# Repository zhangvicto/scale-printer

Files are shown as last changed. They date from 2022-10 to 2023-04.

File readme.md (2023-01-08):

# Particle Swarm Optimization of 3D Printing Parameters on Open-Source Commercial 3D Printer

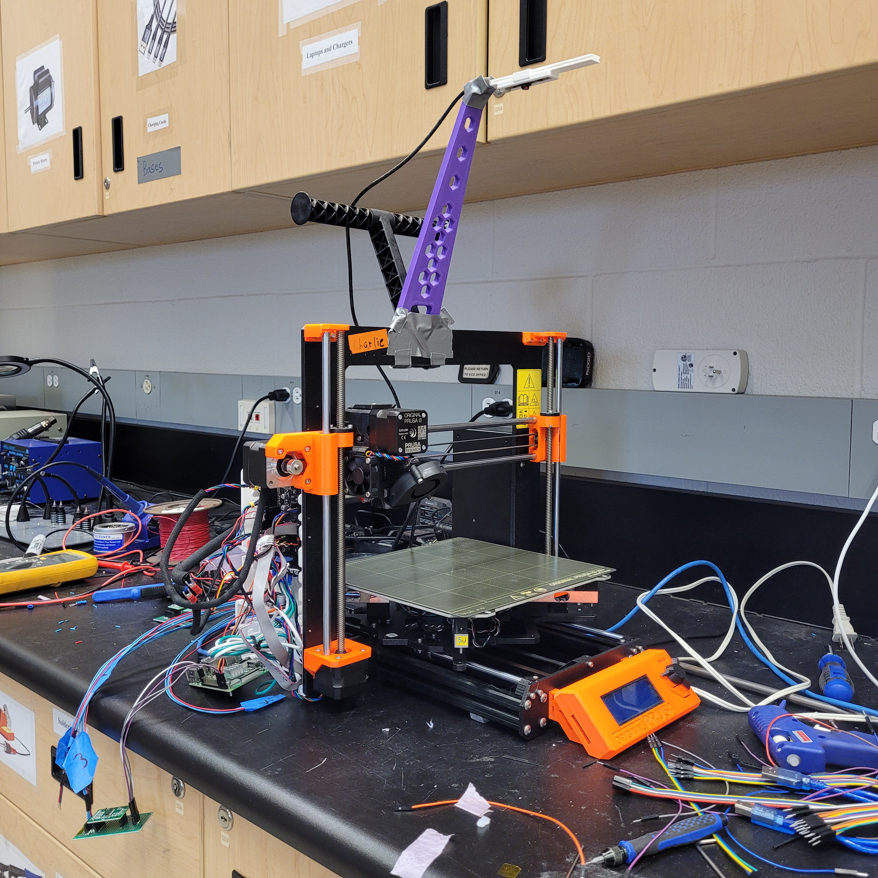
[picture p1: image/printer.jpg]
printer


# Current Progress
- [x] Mechanical Design
- [x] Test Load Cells
- [x] Test Camera
- [ ] Test Dimensional Measurement {80%}
- [ ] PSO Implementation {90%}
- [ ] Documentation {50%}

## Additional Features 
- [ ] Web Server {5%}
- [ ] Refinement {5%}

# Hardware
## Mechanical Design
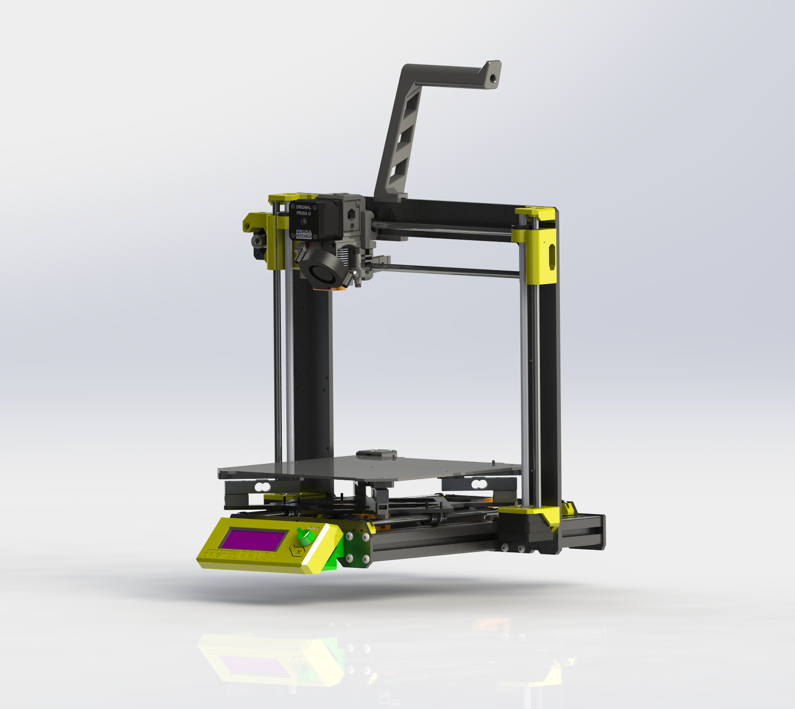
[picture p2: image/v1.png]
v1

The mechanical is designed around the Prusa MK3s, as it is a versatile printer that can be easily modified. Load cells and a camera were mounted on the printer using 3D printed parts. 

Load Cell Configuration: 
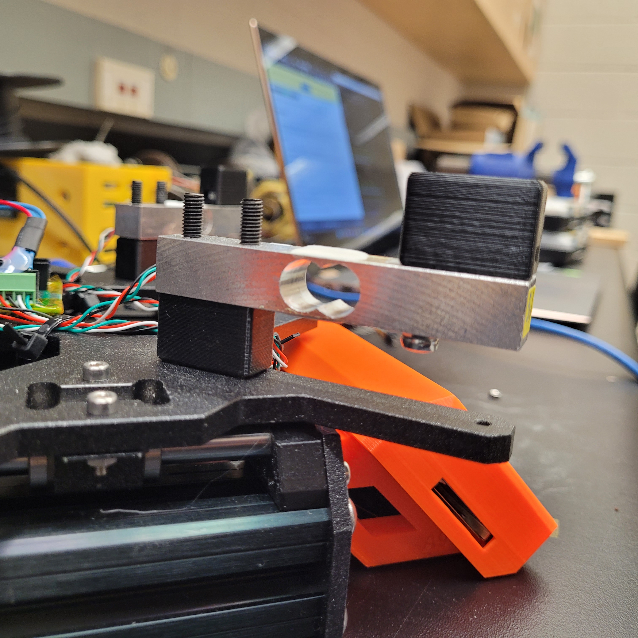
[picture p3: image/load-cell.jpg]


## Bill of Materials
Found in repo. 
Total cost excluding printer is CAD $150.00 (to be updated).

# Software
Flowchart: 
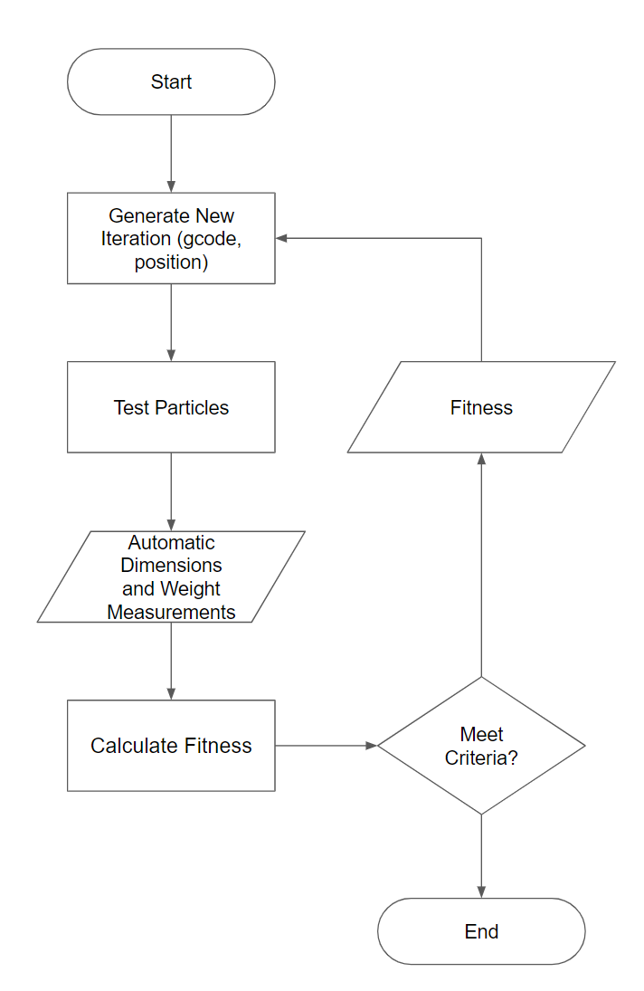
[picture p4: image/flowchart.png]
flowchart


## PSO Algo Implementation
The PSO algorithm runs each calibration sequence by taking an initial guess to generate the first iteration, then using the results of the first iteration to generate the next iteration. The process repeats until the results are desirable or if the max number of iteration is reached. This implementation is adapted from a previous experiment: https://doi.org/10.1089/3dp.2022.0012. 

## Computer Vision
A camera is used to measure the length of each print, as the pixel size can be roughly estimated using the dimension of the bed.
camera

## Load Cell
Load cell measurement is taken and averaged. Measurement is taken after every iteration and used to generate the next iteration. 
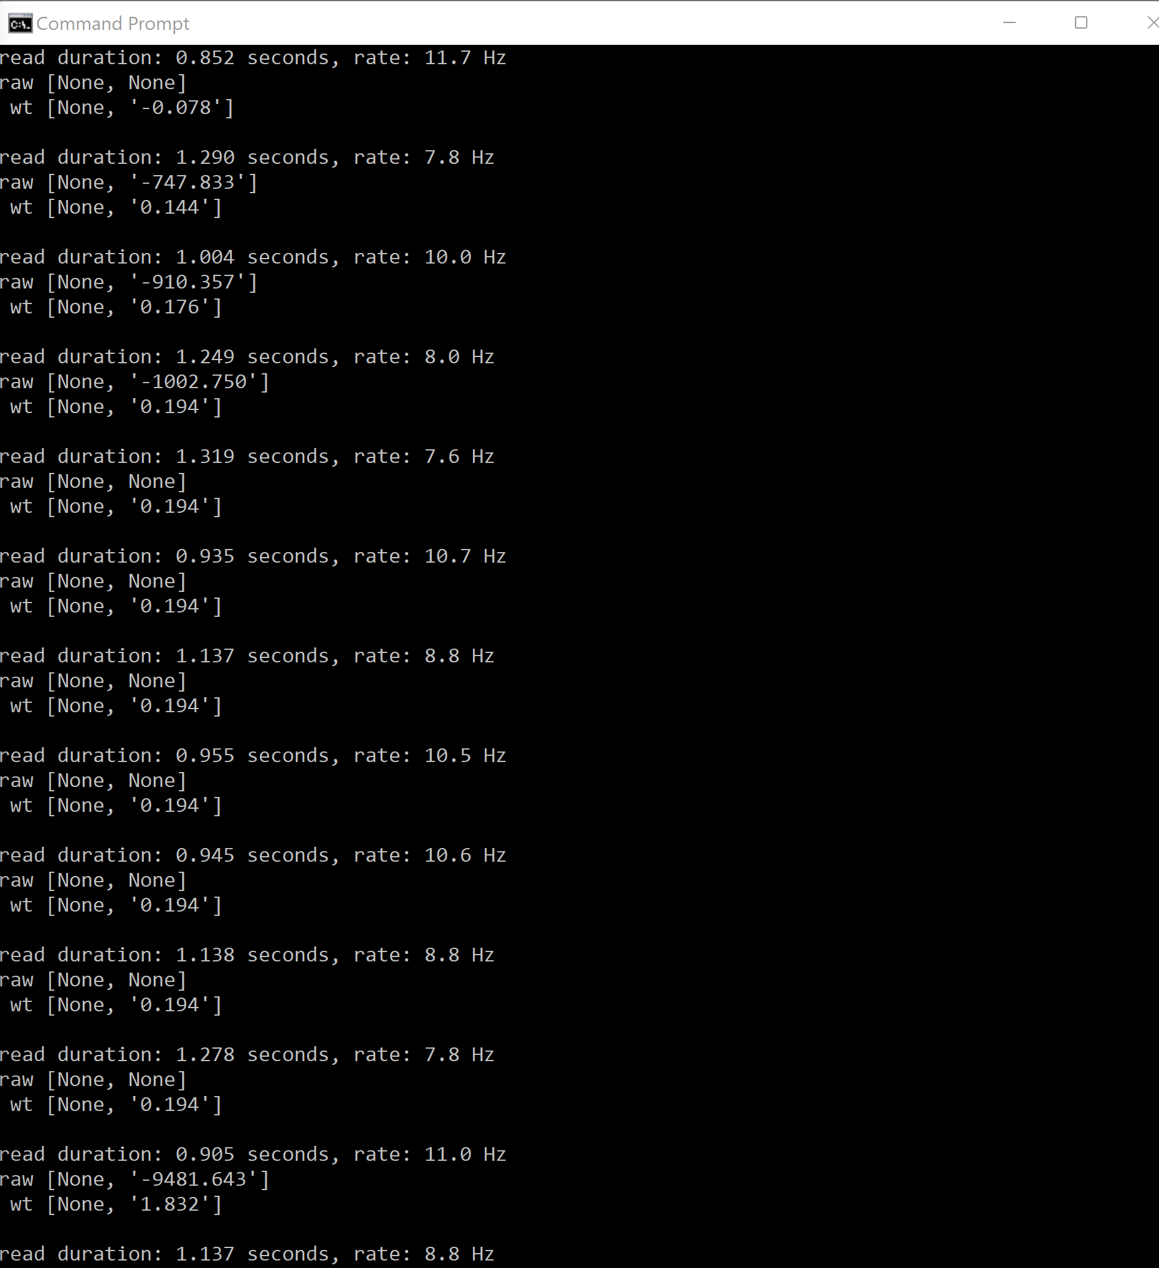
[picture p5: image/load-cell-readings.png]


## Gcode Generation
The Gcode for each interation is generated automatically, using PSO results from the previous run. 

# The Build 
(More detailed instructions in paper in the future)
1. Mount all mechanical components
2. Electrical wiring for all load cells and Raspberry Pi
3. Setup Raspberry Pi with any OS that supports Python
4. git pull repo

## Wiring Diagram 
(coming soon)

# User Instructions

## Requirements
Before running any calibration sequence, the required libraries must be installed for Python. 

If pip is not installed, install it first. 
```
sudo apt-get pip3
```

Then go to the subdirectory where the scripts are located.
```
cd scale-printer/software
```

Run install the requirements using pip.
```
pip3 install -r requirements.txt
```

## Begin Optimization
SSH into the Raspberry Pi and start the script. 
(Assuming you are still in the /softare subdirectory, if not, go to the proper directory)
```
python setup.py
```

Proceed with the instructions. Select your desired calibration method (line, plane, cube). Now just wait and let the printer do its magic!

## Calibrating Sensors
All the load cells will be calibrated before the actual print calibration sequence. Ensure that you are getting correct values for the weights. If they are not right, then there may be wiring or issues with the power supply.  

# Open-Source Licenses
licenses

Thank you to Dr. Joshua Pearce, the Western University FAST Research Lab, and the Thompson Endowment for supporting this project.

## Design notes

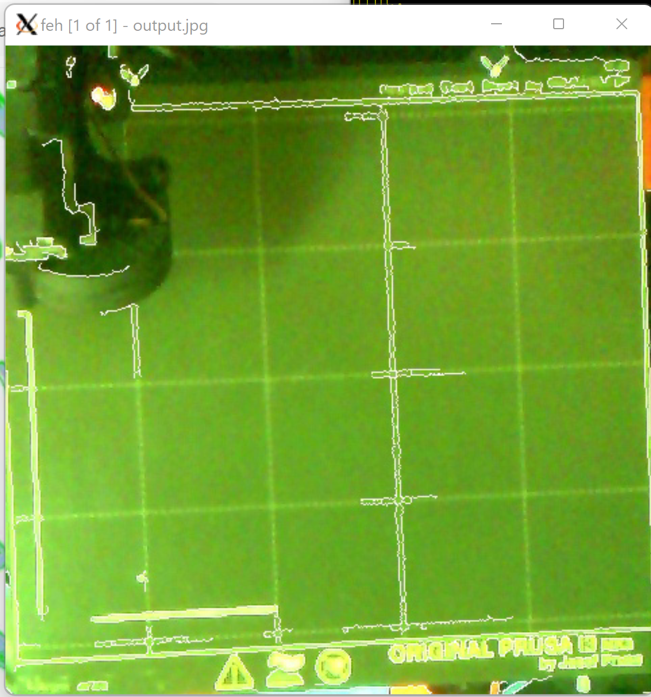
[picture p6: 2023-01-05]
software/cv/example-capture.png

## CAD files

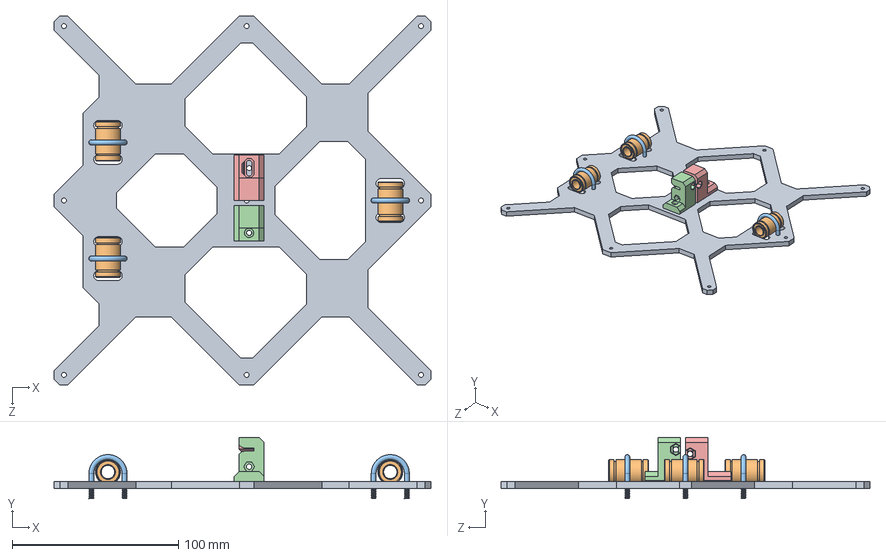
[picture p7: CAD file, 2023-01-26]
CAD/Prusa-i3-MK3S-SW/Frog Assembly.SLDASM
227.0 x 36.8 x 222.0 mm
i3 MK3 Frog
LM8UU x 3
U Bolt x 3
y-belt-holder_R4
y-belt-tensioner_R4

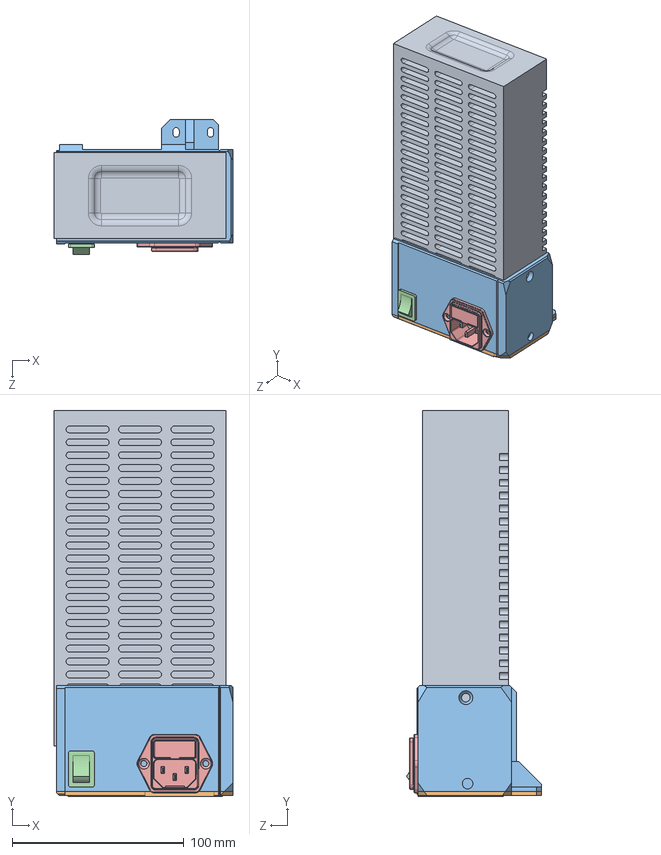
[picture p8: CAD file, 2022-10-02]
CAD/Prusa-i3-MK3S-SW/PSU_Assembly.SLDASM
104.0 x 224.5 x 78.5 mm
PSU_Metal
PSU-cover-MK3_bottom
PSU-cover-MK3_top
PSU_switch
PSU_plug

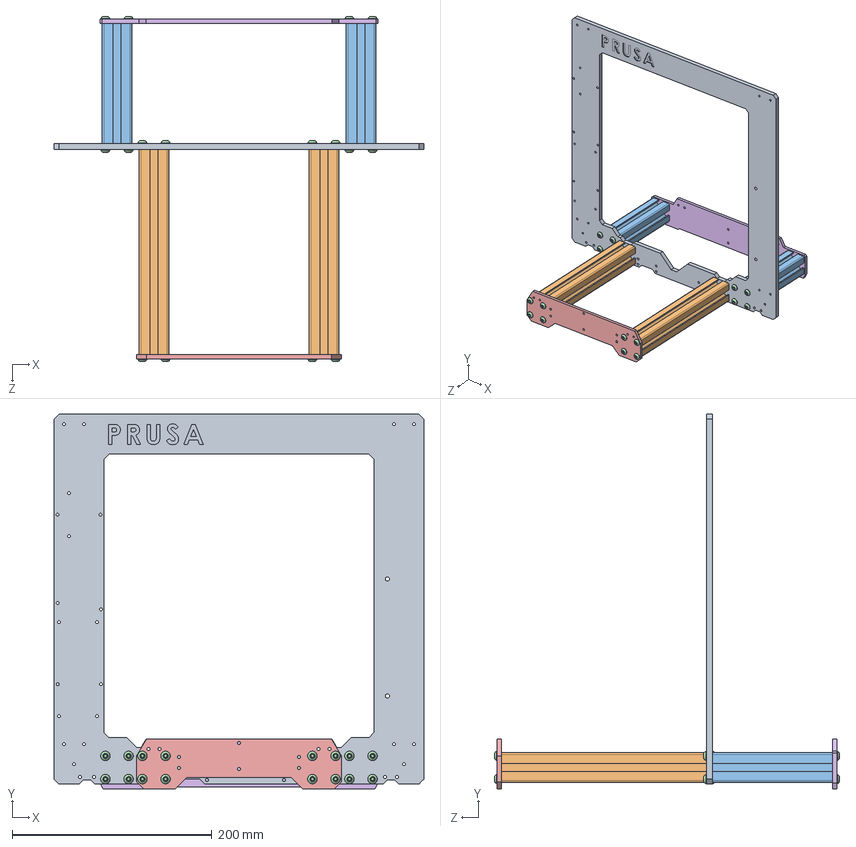
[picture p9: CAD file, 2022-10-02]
CAD/Prusa-i3-MK3S-SW/Frame Assembly.SLDASM
370.0 x 375.0 x 345.2 mm
i3 MK3 Frame
Long Extrusion x 2
Short Extrusion x 2
M5-16 Caphead Screw x 32
MK3 Front Plate
MK3 Rear Plate

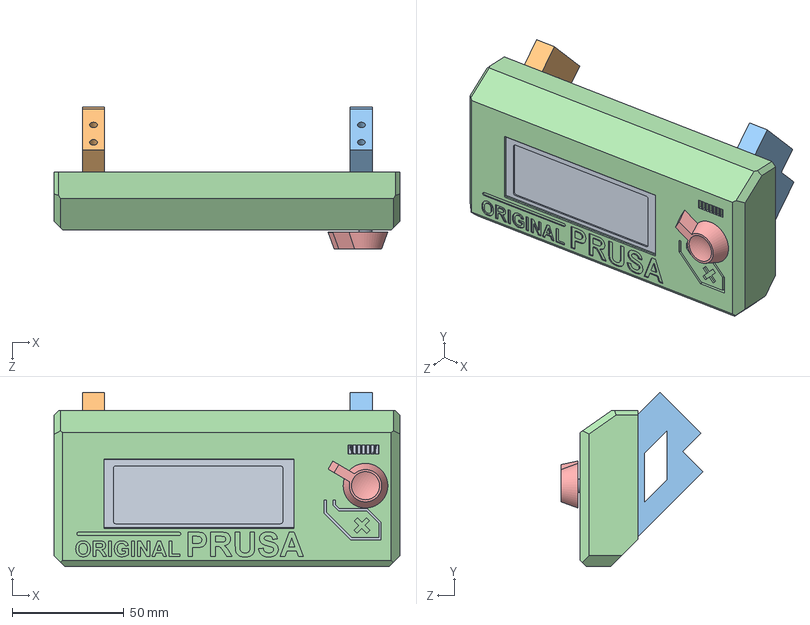
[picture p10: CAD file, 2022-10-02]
CAD/Prusa-i3-MK3S-SW/LCD Assembly.SLDASM
155.0 x 78.2 x 63.5 mm
LCD Board
lcd-supports1
lcd-supports2
LCD-cover-ORIGINAL-MK3(R2)
LCD-knobR2

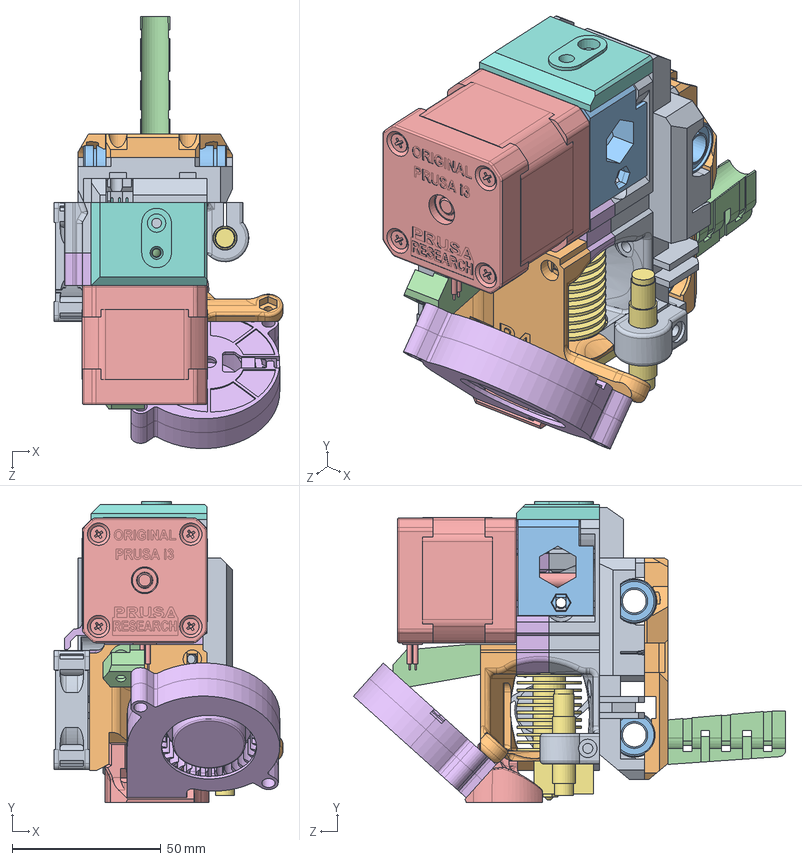
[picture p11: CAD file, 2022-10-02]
CAD/Prusa-i3-MK3S-SW/MK3S Extruder Assembly.SLDASM
77.0 x 101.2 x 145.3 mm
extruder-body_R4
fs-lever
adapter-printer
finda Ball
NEMA-17 40mm PR
extruder-motor-plate_R4
E3D V6
IR-sensor-01
Noctua-NF-A4x10
extruder-cover_R4
extruder-idler_MK3S
print-fan-support_MK3S
fan-shroud_MK3S
Radial-Cooling-Fan-5015-DC12V
PINDA Probe
fs-cover_MK3S
x-carriage_R4
x-carriage-back_R4
LM8UU x 3
cable-holder

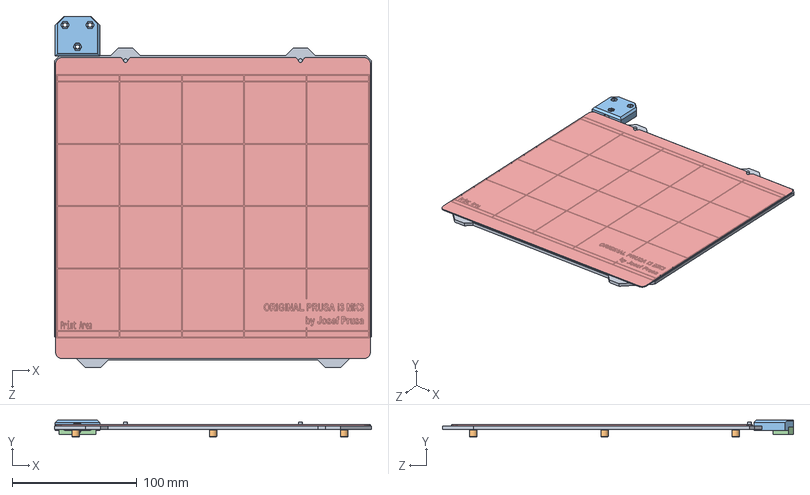
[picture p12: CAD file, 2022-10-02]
CAD/Prusa-i3-MK3S-SW/Headbed Assembly.SLDASM
253.8 x 13.6 x 281.4 mm
MK52 Bed
6x6x3t spacer x 9
heatbed-cable-cover top
heatbed-cable-cover bottom

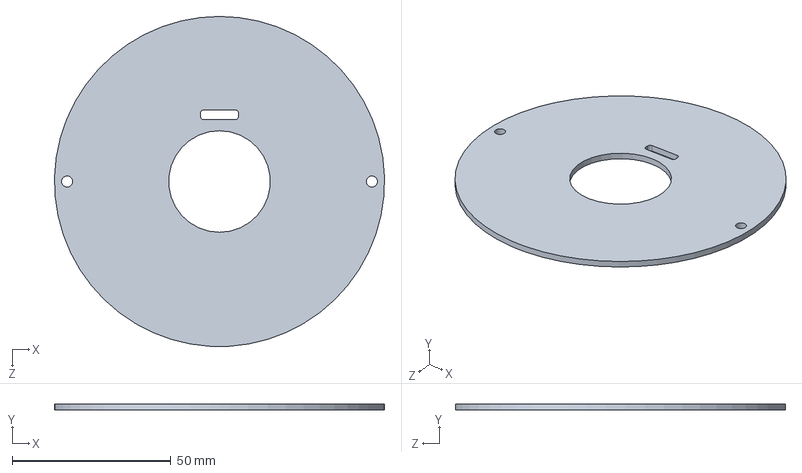
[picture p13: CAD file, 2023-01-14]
CAD/camera-mount-new/light-cover.SLDPRT
104.0 x 2.00 x 104.0 mm

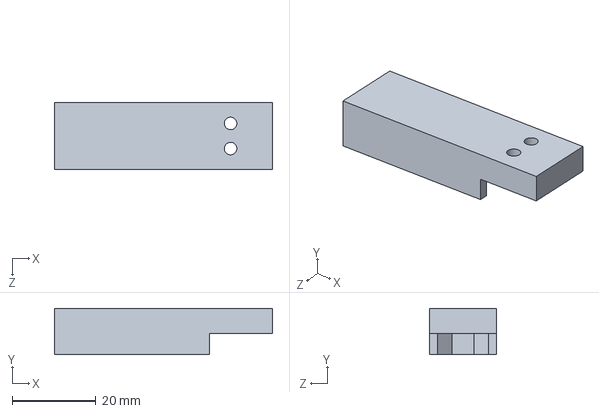
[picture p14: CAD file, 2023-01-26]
CAD/drill-guide.SLDPRT
52.0 x 11.0 x 16.1 mm

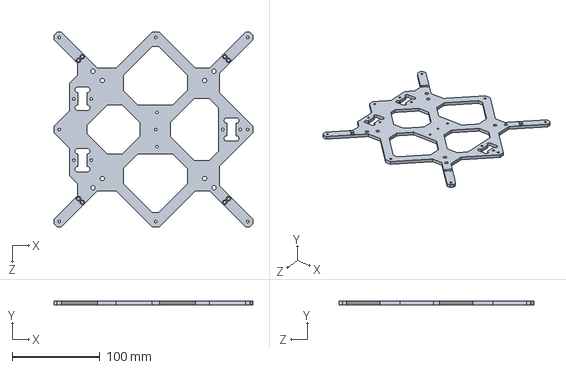
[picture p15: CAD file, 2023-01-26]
CAD/Prusa-i3-MK3S-SW/i3 MK3 Frog.SLDPRT
227.0 x 4.25 x 222.0 mm

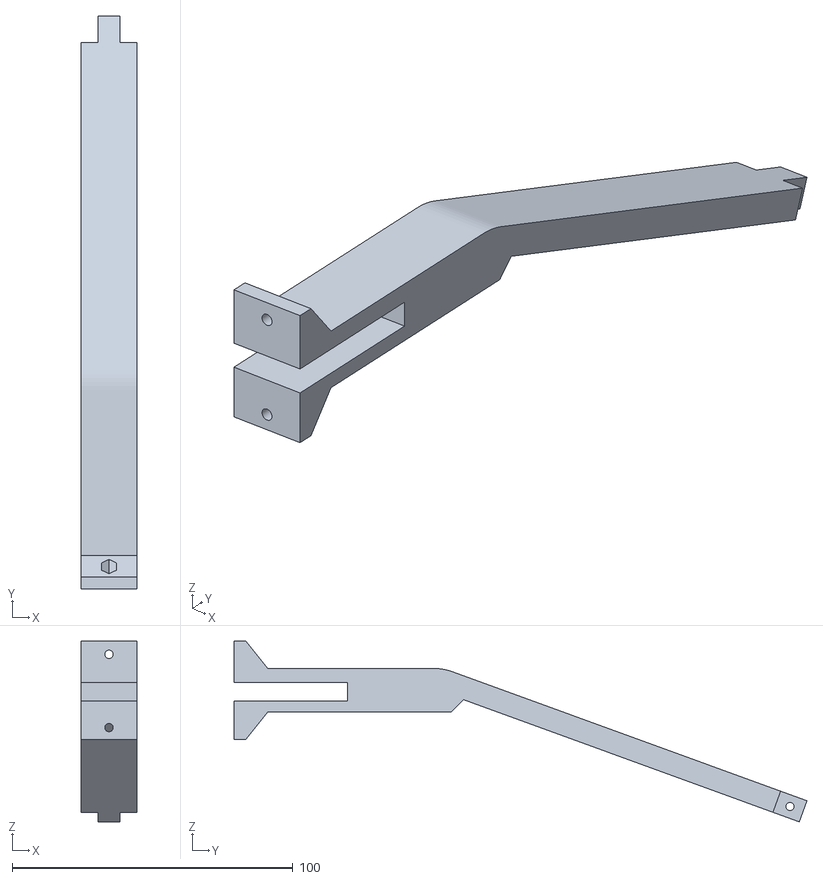
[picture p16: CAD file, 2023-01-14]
CAD/stl/camera-mount-one-piece-p2.STL
20.0 x 204.1 x 64.4

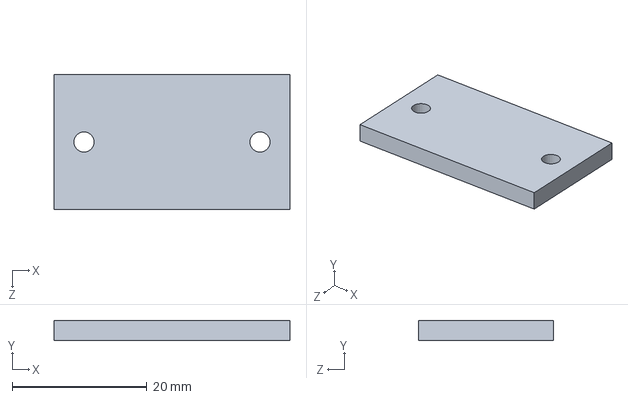
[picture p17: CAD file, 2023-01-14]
CAD/camera-mount-new/camera-mount-clip.SLDPRT
35.0 x 3.00 x 20.0 mm

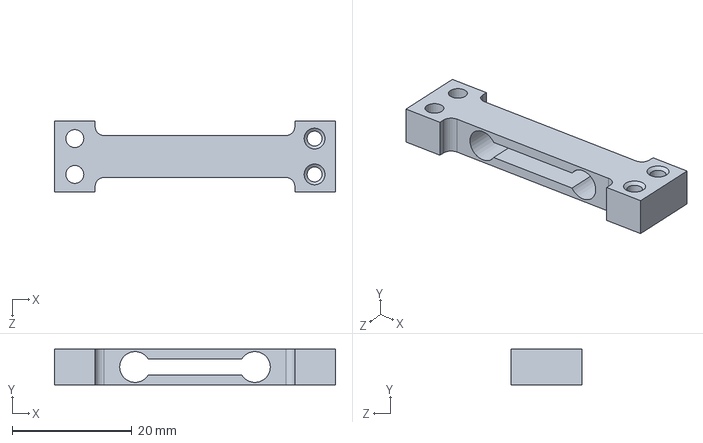
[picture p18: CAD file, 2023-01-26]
CAD/load-cell-100g.SLDPRT
47.0 x 6.00 x 11.9 mm

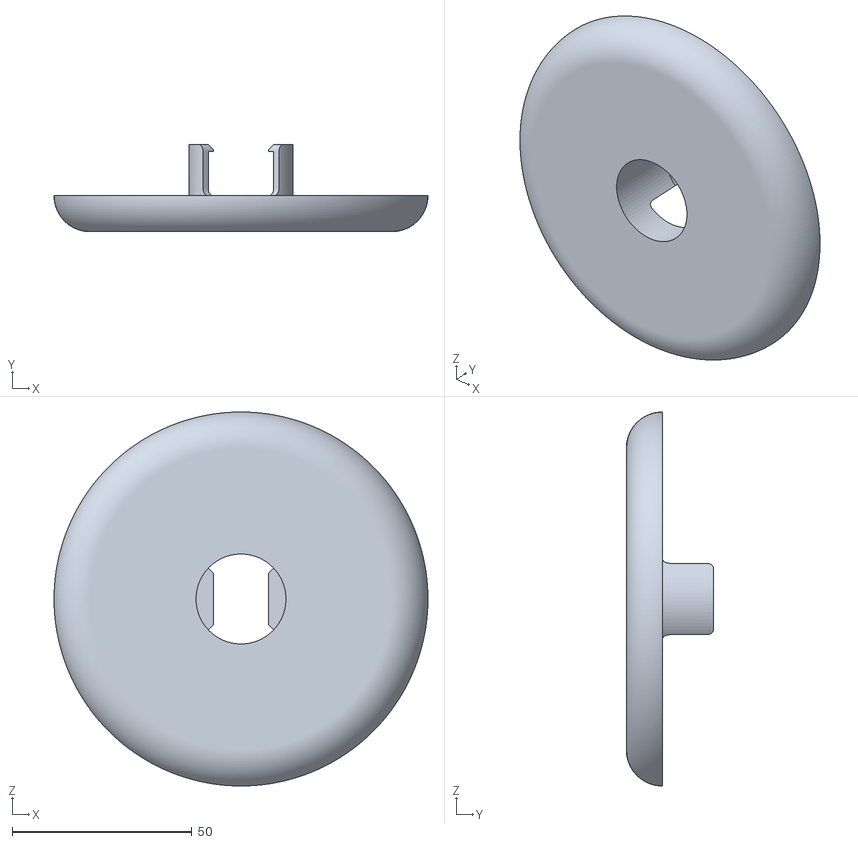
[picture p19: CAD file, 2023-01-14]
CAD/stl/light-fixture.STL
104.0 x 24.3 x 104.0

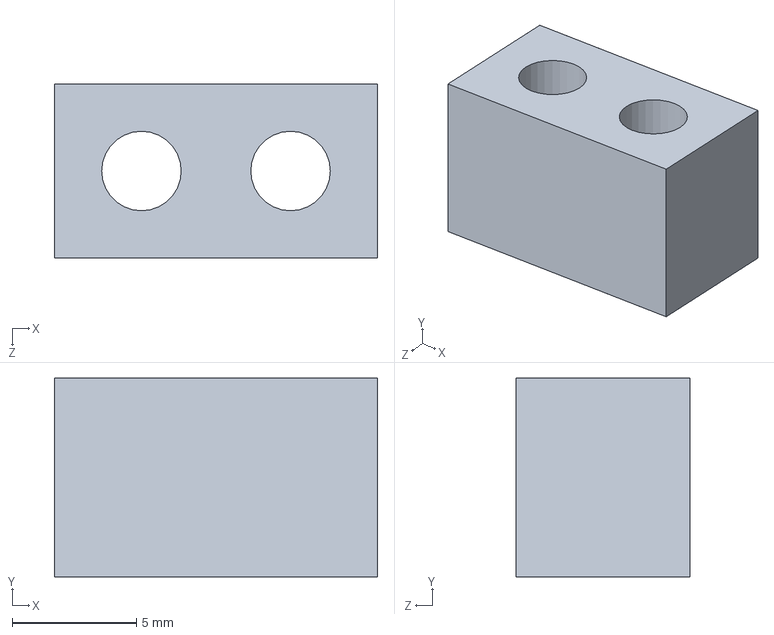
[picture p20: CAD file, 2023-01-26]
CAD/bed-spacer.SLDPRT
13.0 x 8.00 x 7.00 mm

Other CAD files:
CAD/camera-mount-new/camera-mount-one-piece-p2.SLDPRT
CAD/Prusa-i3-MK3S-SW/extruder-motor-plate_R4.SLDPRT
CAD/stl/camera-mount-one-piece-p1.STL
CAD/bed-mount.SLDPRT
CAD/DEPRECATED/camera-mount-link-2.SLDPRT
CAD/DEPRECATED/camera-mount-main-link.SLDPRT
CAD/DEPRECATED/heated-bed-mount-right.SLDPRT
CAD/DEPRECATED/heated-bed-mount.SLDPRT
CAD/DEPRECATED/load-cell-5kg.SLDPRT
CAD/DEPRECATED/spacer-bed.SLDPRT
CAD/DEPRECATED/spacer.SLDPRT
CAD/Prusa-i3-MK3S-SW/6x6x3t spacer.SLDPRT
CAD/Prusa-i3-MK3S-SW/E3D V6.SLDPRT
CAD/Prusa-i3-MK3S-SW/Einsy Base 2.SLDPRT
CAD/Prusa-i3-MK3S-SW/Einsy-hinges1.SLDPRT
CAD/Prusa-i3-MK3S-SW/Einsy-hinges2.SLDPRT
CAD/Prusa-i3-MK3S-SW/IR-sensor-01.SLDPRT
CAD/Prusa-i3-MK3S-SW/Idler Roller, flat.SLDPRT
CAD/Prusa-i3-MK3S-SW/LCD Board.SLDPRT
CAD/Prusa-i3-MK3S-SW/LCD-cover-ORIGINAL-MK3(R2).SLDPRT
CAD/Prusa-i3-MK3S-SW/LCD-knobR2.SLDPRT
CAD/Prusa-i3-MK3S-SW/LM8UU.SLDPRT
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

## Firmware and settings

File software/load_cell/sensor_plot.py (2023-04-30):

import matplotlib.pyplot as plt
from hx711_multi import HX711
from time import perf_counter, sleep
import RPi.GPIO as GPIO  # import GPIO
import numpy as np

# init GPIO (should be done outside HX711 module in case you are using other GPIO functionality)
GPIO.setmode(GPIO.BCM)  # set GPIO pin mode to BCM numbering

readings_to_average = 10
sck_pin = 6
dout_pins = [22, 4, 17, 27] # 1, 2, 3, 4
weight_multiples = [6561.210267857154, 6155.000297619006, 5987.672569444473, 6004.160069444496] # 128 gain

# create hx711 instance
hx711 = HX711(dout_pins=dout_pins,
              sck_pin=sck_pin,
              channel_A_gain=64,
              channel_select='A',
              all_or_nothing=False,
              log_level='CRITICAL')
# reset ADC, zero it
hx711.reset()
sleep(0.2)
hx711.reset()

# Try Zeroing ADC
try:
    hx711.zero(readings_to_average)
except Exception as e:
    print(e)

# Set multiple 
hx711.set_weight_multiples(weight_multiples=weight_multiples)

measurements = []
cell1 = []
cell2 = []
cell3 = []
cell4 = []
time = []

# separate each cell into its own array of measurements 

# plot all with legends 
plt.plot([cell1, time])
plt.ylabel('Mass (g)')
plt.xlabel('Time (s)')

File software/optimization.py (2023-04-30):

from pso.optimize_helpers import Particle, accuracy, consist
# import numpy as np
from load_cell.mass import measure_mass, tare
from gcode_gen.generate import gcode_gen, genStart, genEnd, square_size
from gcode_sender.printcore_gcode_sender import send_gcode
from cv.dimensions import image_process, edges, analyze_edge, find_dim
from time import perf_counter

# Settings
numParticles = 10

# Execute iteration
def optimize(mode, xmax, xmin, xguess, mass_desired, numDimensions, iteration): #inputs should be the fitness of last iteration
    
    # global optimum
    particles = []
    mass_data = []
    dimension_data = []
    x_best_g = []

    # Create Particle Array
    for i in range(0, numParticles):
        # Add new particle to particle array
        particle = Particle(xmax, xmin, xguess, numDimensions)
        particles.append(particle)

    # STARTING THE ITERATION
    
    # For each particle, print and collect data
    particle_i = 0 # particle index

    last_mass = 0 

    for particle in particles:

        iter = particle_i + 1
        time_start = perf_counter()


        # MEASUREMENT STUFF

        # creep = 0.0005*5000/(3*60)*4 # grams/sec * 4 load cells

        zero_weight = 0 

        # Taring
        if iter == 1: 
            zero_weight = tare()
        # print("Initial weight offset: {}".format(zero_weight))

        # Account for Creep - ignoring creep for now
        initial_zero = zero_weight #- time_zero*creep


        # Generate Gcode
        with open("./gcode_gen/test.gcode", "w") as f:
            
            gcode = genStart(iter=iter, nozzleD=0.4, Te=xguess[0], Tb=0) # bed is disabled
            gcode += gcode_gen(mode, iter, {'moveSpeed': xguess[1], 'extMult': xguess[2]}) # generate gcode with custom parameters
            gcode += genEnd()

            f.write(gcode)
        
        print("Gcode Generated. \n")

        # Tare Weight before Starting Print
        # time_zero = perf_counter() - time_start
        # print("Initial weight offset: {}".format(time_zero))

        # Pass in Printing Parameters
        print("Sending Gcode to Printer. \n")
        send_gcode(iter, './gcode_gen/test.gcode')

        # measure_time = perf_counter() - time_zero

        # Once print finishes, check weight
        print("Measuring Mass. \n")
        mass = measure_mass()
        mass_real = mass - last_mass - initial_zero # find weight of print
        mass_data.append(mass_real)

        last_mass = mass


        # CV STUFF

        # Find Dimension of the Print
        print("Starting CV Process. \n")
        img = image_process() # Process Image
        edge = edges(img) # Canny Edge Detection

        distX = analyze_edge(edge) # Get the bed x-axis length in terms of pixels

        x=[]
        y=[]

        # Calculate Print Location
        if distX is not None:
            ratio = distX/255 # Pixels per mm
            print('Ratio: {}'.format(ratio))
            # Pixel = mm * ratio

            if mode == 'L': 
                if distX > 0: 
                    xOffset = 20
                    x1 = xOffset + round((iter-1)*15*ratio)
                    x2 = round(x1 + 10*ratio)
                    x = [x1, x2]
                    # print(x)
                    # print(x)
                    y1 = round(180*ratio) - 20
                    y2 = round(180*ratio)
                    y = [y1, y2]
                else: 
                    x = [None, None]
                    y = [None, None]

            if mode == 'P': 
                if distX: 
                    initial_gap = 10
                    gap = 10
                    x1 = round((initial_gap + gap/2 + (iter-1)*square_size)*ratio)
                    x2 = round(x1 + (square_size + gap)*ratio)
                    x = [x1, x2]
                    # print(x)
                    yOffset = -5
                    y1 = round((200 - (square_size + gap + yOffset))*ratio)
                    y2 = round((200- yOffset)*ratio)
                    y = [y1, y2]
                    # print(y)
                else: 
                    x = [None, None]
                    y = [None, None]
            
            if mode == 'C': 
                x = [None, None]
                y = [None, None]

        dimensions = find_dim(x, y, distX, edge, iter) # Find dim

        if dimensions is not None: 
            widths = dimensions[0]
            lengths = dimensions[1]
            dimension_data.append(dimensions)
        else: 
            dimension_data.append(None)
        
        # Print all data
        print("Mass: {}. Dimensions: {}. Time Elasped: {}.".format(mass_data, dimension_data, perf_counter() - time_start))


        # PSO STUFF

        # Evaluate and compare particle global optimum to local optimum
        # Calculate Current Fitness
        particle.f_best_p = fitness(mode, dimensions[0], dimensions[1], mass, mass_desired, square_size, square_size)
        print("Fitness: {}".format(particle.f_best_p))

        if iter == 1:
            x_best_g = particle.x_best_p[:] # Set global optimum to first particle
            f_best_g = particle.f_best_p # set global optimum to first particle
        else: 
            if particle.f_best_p < f_best_g: # Compare particle fitness to group fitness
                x_best_g = particle.x_best_p[:] # Splice array and set global op to current particle

        # Generate new values for the next iteration based on previous iteration
        particle.updateVelocity(x_best_g)
        particle.updatePosition()

        print("Particle Position: {}".format(particle.x_best_p))
        
        # NEXT PARTICLE
        particle_i += 1

    print('Iteration {} complete.'.format(iteration))

    return particle.x_best_p


# Fitness Functions
def fitness(mode, widths, lengths, mass, mass_desired, width_desired, length_desired): # width is a list of measurements for the plane or cube
    if mode == "L": 
        return 0.2*consist([widths, lengths]) + 0.2*accuracy(average(widths), width_desired)+ 0.1*accuracy(average(lengths), length_desired) + 0.5*accuracy(mass, mass_desired)

    elif mode == "P": 
        return 0.1*accuracy(widths, width_desired)+ 0.1*accuracy(lengths, length_desired) + 0.7*accuracy(mass, mass_desired)
    
    elif mode == "C":
        return 0
    
def average(list): 
    for i in list: 
        sum =+ i
    
    return sum/list.len()

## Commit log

2022-10-02 Push CAD v1
    [6x6x3t spacer.SLDPRT, E3D V6.SLDPRT, Einsy Base 2.SLDPRT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]
2022-10-05 Change Spacer Location
    [Frog Assembly.SLDASM, i3 MK3 Frog.SLDPRT, spacer-bed.SLDPRT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]
2022-11-29 PSO Changes
    [Frog Assembly.SLDASM, i3 MK3 Frog.SLDPRT, load-cell-5kg.SLDPRT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]
2022-12-22 Changed Pin, test gcode sending
2023-01-06 Update Spacer, add more PSO code
    [spacer-new.STL, spacer.SLDPRT]
2023-01-06 Add load cell calibration
2023-01-07 Add Calibrate all for load cells
2023-01-08 Test print
2023-01-10 Update Dim
    [light-fixture.SLDPRT]
2023-01-12 Load Cell Calibration
2023-01-12 Update Calibration
2023-01-14 Semi Final Update
    [camera-enclosure.STL, camera-mount-clip.SLDPRT, camera-mount-clip.STL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]
2023-01-26 Update Load Cell Calibration Values
2023-02-01 Update - hopefully fixing error
    [calibration_setup.py, optimization.py, printcore_gcode_sender.py]
